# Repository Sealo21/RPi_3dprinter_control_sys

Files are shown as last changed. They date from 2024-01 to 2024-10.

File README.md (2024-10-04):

# RPi_3dprinter_control_sys
Environment controller for a 3D printing enclosure using a Raspberry Pi. \
Uses a temperature/VOC sensor and a custom PCB controller for the fans and strip LEDs controlled by a Raspberry Pi. \
This project is a work-in-progress. It is functional...but still a beta.

# Components
  - Raspberry Pi 4 Model B  
  - [Sensirion Particle, VOC, Humidity, and Temperature Sensor](https://www.sparkfun.com/products/23715)  
  - [waveshare 4 inch HDMI LCD 800x480](https://www.amazon.com/gp/product/B07P5H2315/)  
  - [Geekworm GPIO Extender](https://www.amazon.com/gp/product/B0BDF48FWM/)  
  - [SamIdea 2-Pack 40pin Male to Female IDC GPIO](https://www.amazon.com/gp/product/B07CGM83QL/)  
  - [Micro HDMI Cable](https://www.sparkfun.com/products/15796)  
  - Any 2 or 4 pin PC fan [I am using Noctua NF-A8 PWM](https://noctua.at/en/nf-a8-pwm)  
  - Any SMD5050 strip LED [LED Strip Lights](https://www.amazon.com/gp/product/B08JSQVBDQ/)

# Software Installation

[Install the latest version of Raspian OS](https://projects.raspberrypi.org/en/projects/raspberry-pi-setting-up) on your Raspberry Pi \
[Edit your configuration](https://www.raspberrypi.com/documentation/computers/configuration.html) to enable 'I2C' and 'Remote GPIO' under the interfaces tab \
Save and restart your RPi 

Update packages to the latest version:
```command line
sudo apt update
```

1. Download the files marked "RPi_3dprinter_control_sys_main" 
2. Locate the file 'main' in the folder 'dist' 
3. Edit the properties of 'main' to open with the program 'Terminal' 
4. Set the permission "Execute" to 'Anyone' 
5. If you run the program without modifying these settings a pop-up may occur asking to run the executable with an application 
6. Once these settings are confirmed the program should start with a terminal followed by a window

# Hardware Setup

A GPIO Extender will be needed to have the screen and GPIO be plugged in at the same time. 

There are a few options for the hardware of your controller \
A cheap option is to breadboard the design using the design schematics from the file 'LED_FAN_CONTROLLER.kicad_sch' \
You may need to download and install Kicad to view this schematic.

Here are the design requirements to breadboard this project:
- 4 [IRL520](https://www.digikey.com/en/products/detail/vishay-siliconix/IRL520PBF/811718) Mosfets as a substitute for the [IRLL014TRPBF](https://www.digikey.com/en/products/detail/vishay-siliconix/IRLL014TRPBF/811425)
- Wire for connections
- 6 10k Ohm resistors
- 5 1k Ohm resistors
- In testing phase for 3.3V power controller for breadboarding. I have been testing using an ADALM2000
- Using [TC74HC04APF](https://www.digikey.com/en/products/detail/toshiba-semiconductor-and-storage/TC74HC04APF/870457) for PWM operations in breadboard testing

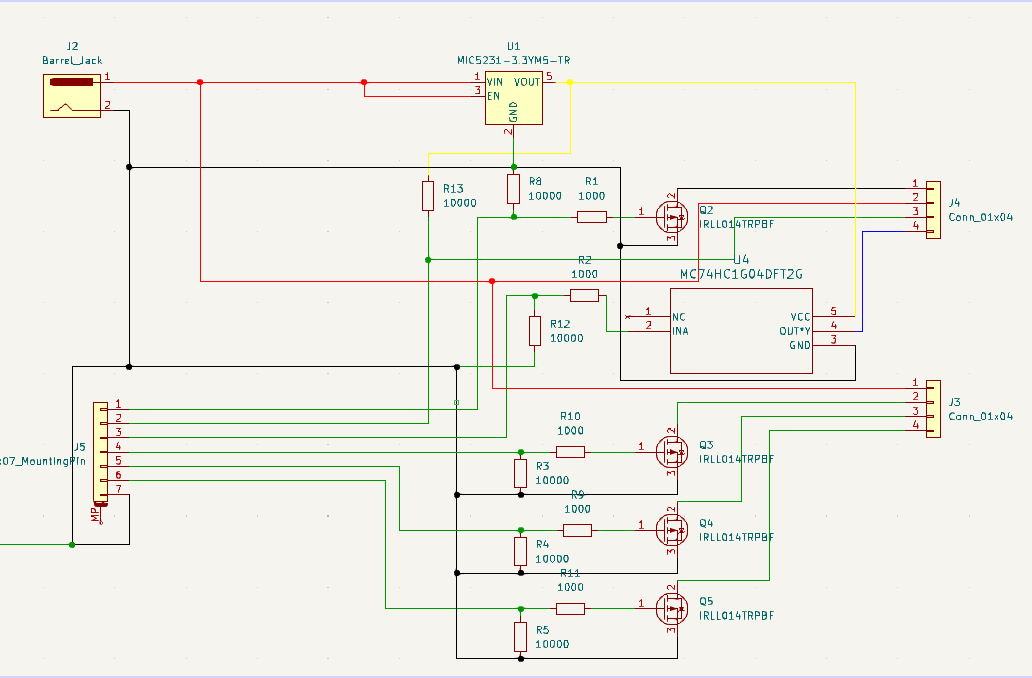
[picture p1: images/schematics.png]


The other option is to use the PCB schematics and manufacture the PCB. \
I have not done this yet as I am working on an upgrade to the current version.

# Touchscreen

Your experience may change based on which touchscreen is used. \
Use xinput-calibrator to calibrate the touch screen. 

```
sudo apt-get install xinput-calibrator
```
You will find this program under Menu -> Preferences -> Calibrate Touchscreen. \
Follow the instuctions given in the command line to save the calibration.

If the system does not recognize the touchscreen, check with the manufacturer for driver files. 

# Installing the Sen55 Sensor

The sensors I recieved do not have a standard coloring scheme. \
I have made a table below to list where the pins must go and their color.

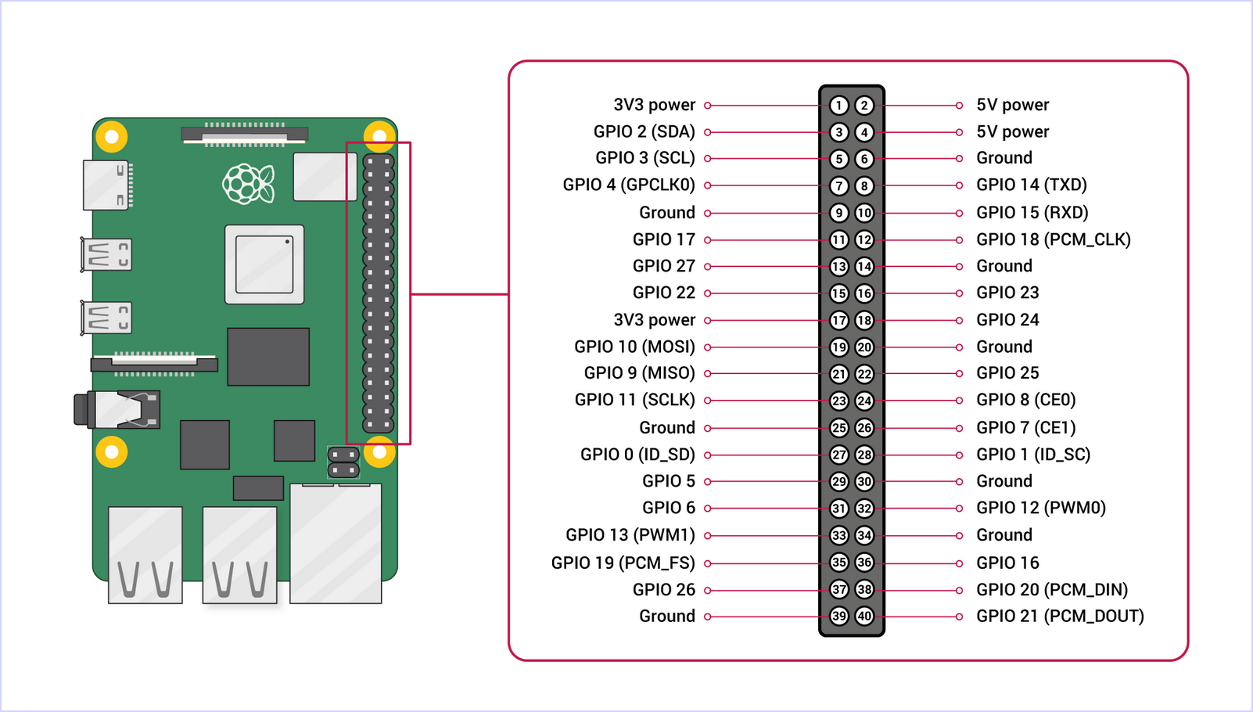
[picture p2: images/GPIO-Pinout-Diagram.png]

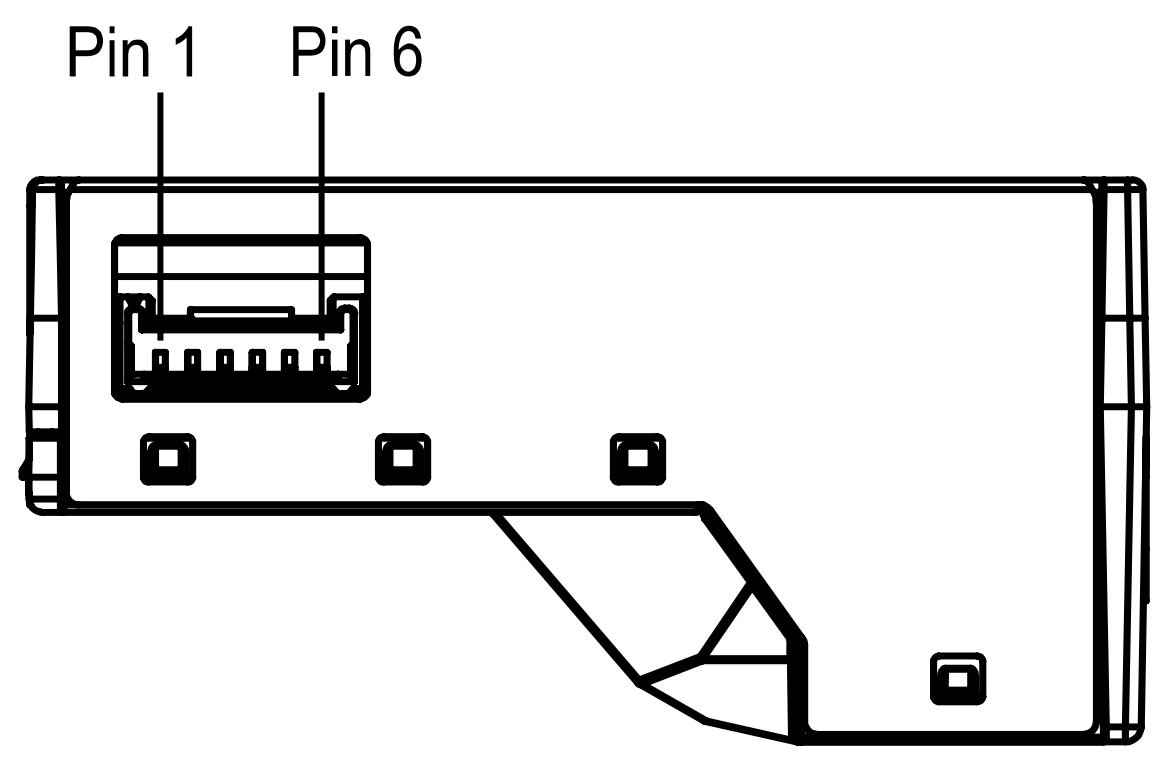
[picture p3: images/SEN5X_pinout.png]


|  Pin (On Sensor) |  Name |  Description |  Color  |  Pin Placement (On RPi)  |
| --- |:---:|:---:|:---:|:---:|
|  1 |  VCC | Supply Voltage  | Green |  Pin 2 (5V) |
|  2 |  GND | Ground | Blue |  Pin 6 (GND) |
|  3 |  SDA | I2C: Data | Yellow  |  Pin 3 (SDA) |
|  4 |  SCL | I2C: Clock | Black |  Pin 5 (SCL) |
|  5 |  SEL | Interface Select| Red |  Pin 9 (GND) |
|  6 |  NC | Do Not Connect  | Brown |  NC |

If the device is not recognized by the system, connect the VCC to 3.3V pin and then back to 5V. \
The device can function on both 3.3V and 5V but 5V is recommended by the manufacturer. \
Use the i2cdetect command to check connected I2C devices.

```command line
i2cdetect -y 1
```

You should see a device listed with a number value.

More information about this installation can be found [here](https://github.com/Sensirion/raspberry-pi-i2c-sen5x)

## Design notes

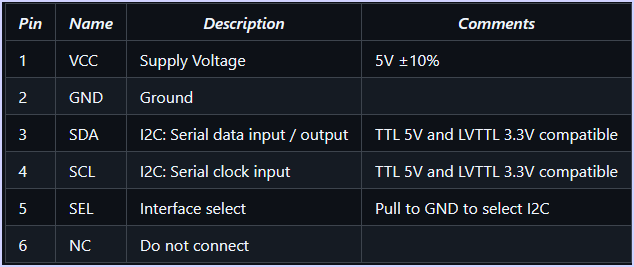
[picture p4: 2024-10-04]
images/Screenshot 2024-10-03 214042.png

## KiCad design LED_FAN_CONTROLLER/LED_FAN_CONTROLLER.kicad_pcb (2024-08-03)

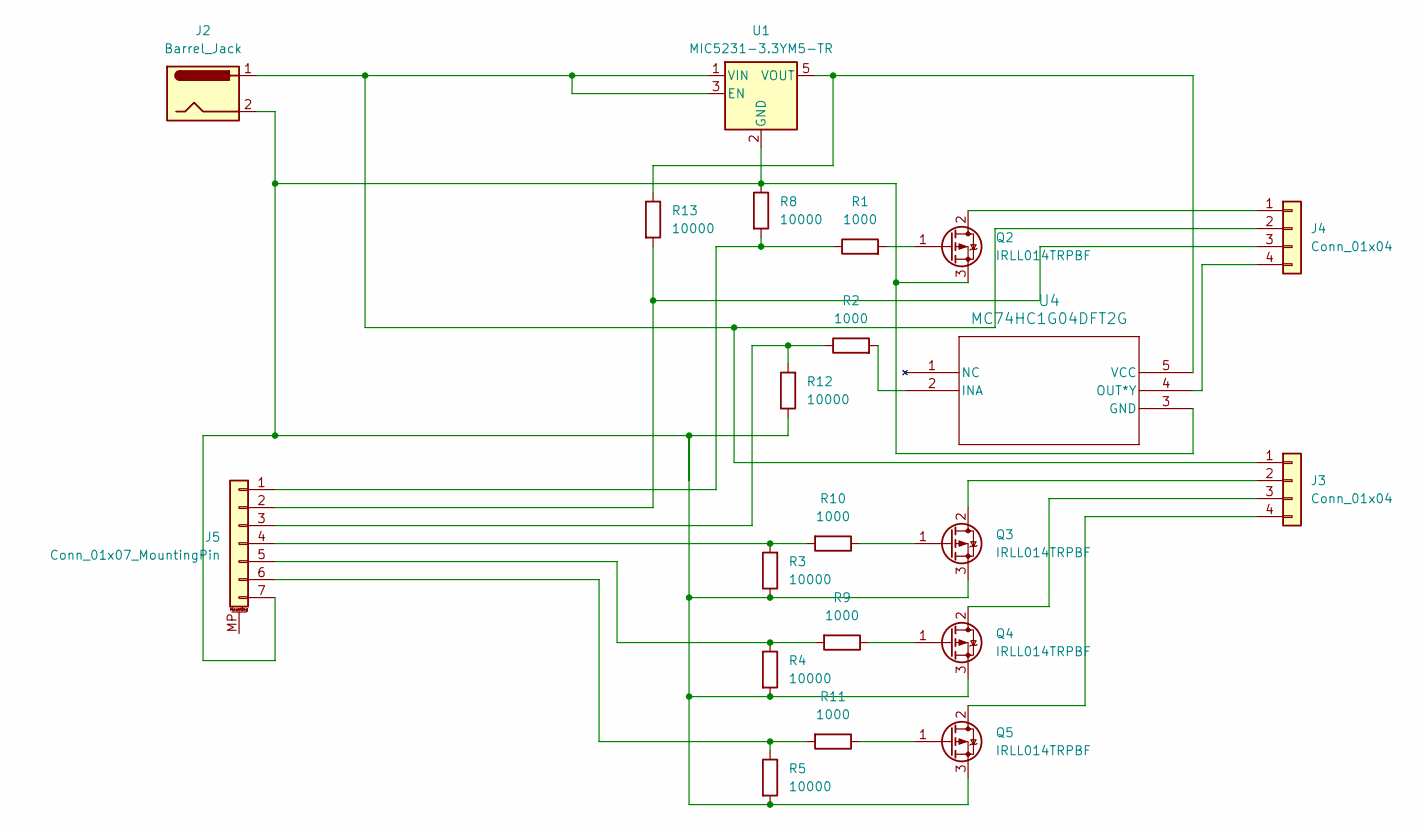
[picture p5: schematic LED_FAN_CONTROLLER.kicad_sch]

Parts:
J2: Barrel_Jack; BarrelJack_Horizontal
J3: Conn_01x04; PinHeader_1x04_P2.54mm_Horizontal
J4: Conn_01x04; FanPinHeader_1x04_P2.54mm_Vertical
J5: Conn_01x07_MountingPin; PinSocket_1x07_P2.54mm_Vertical
Q2, Q3, Q4, Q5: IRLL014TRPBF; SOT-223-3_TabPin2
R1, R2, R9, R10, R11: 1000; R_0603_1608Metric
R3, R4, R5, R8, R12, R13: 10000; R_0603_1608Metric
U1: MIC5231-3.3YM5-TR; SOT-23-5
U4: MC74HC1G04DFT2G; SC70-5_ONS

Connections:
unnamed: J2.1, J3.1, J4.2, U1.1 (VIN), U1.3 (EN)
unnamed: J3.2, Q3.2 (D)
unnamed: J3.3, Q4.2 (D)
unnamed: J3.4, Q5.2 (D)
unnamed: J4.1, Q2.2 (D)
unnamed 5: J4.3, J5.2, R13.2; also elsewhere on the board
unnamed 6: J4.4, U4.4 (OUT*Y); also elsewhere on the board
unnamed: J5.1, R1.1, R8.2
unnamed: J5.3, R2.1, R12.2
unnamed: J5.4, R3.2, R10.2
unnamed: J5.5, R4.1, R9.2
unnamed: J5.6, R5.1, R11.2
unnamed 12: J2.2, J5.7, Q2.3 (S), Q3.3 (S), Q4.3 (S), Q5.3 (S), R3.1, R4.2, R5.2, R8.1, R12.1, U1.2 (GND), U4.3 (GND); also elsewhere on the board
unnamed: Q2.1 (G), R1.2
unnamed: Q3.1 (G), R10.1
unnamed: Q4.1 (G), R9.1
unnamed: Q5.1 (G), R11.1
unnamed 17: R13.1, U1.5 (VOUT), U4.5 (VCC); also elsewhere on the board
unnamed: R2.2, U4.2 (INA)

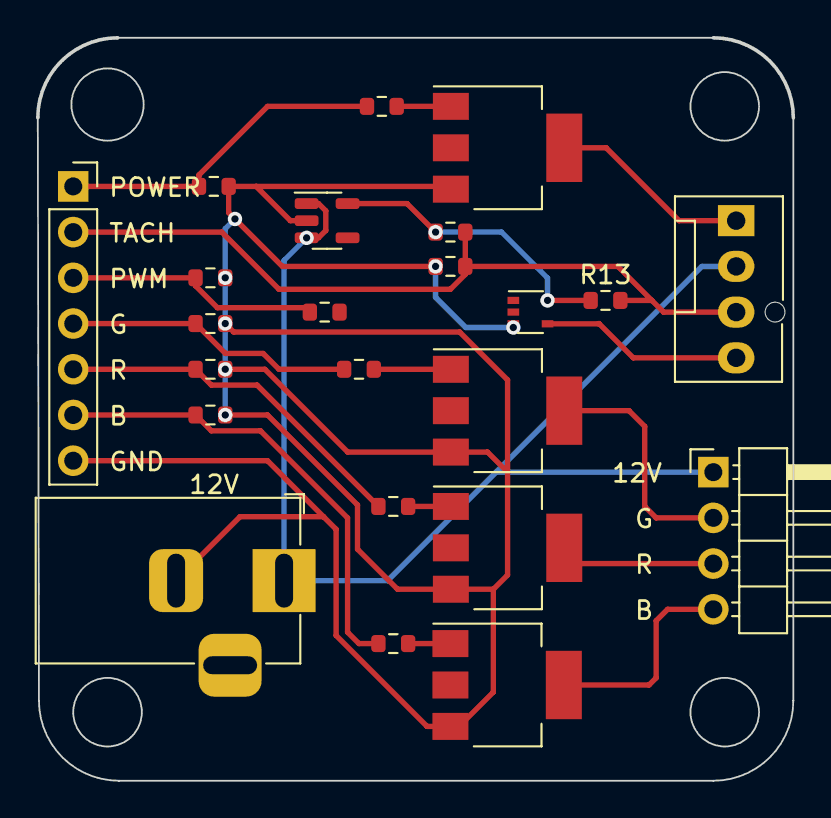
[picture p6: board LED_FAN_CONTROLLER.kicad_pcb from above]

Board: 2 copper layers, 42.0 x 41.3 mm, 23 parts (0 on the bottom side), 18 nets.

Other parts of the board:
R6: 1700; R_0603_1608Metric
R7: 3300; R_0603_1608Metric
U2: MC74HC1G04DFT2; SOT-353_SC-70-5

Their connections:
unnamed 5: R6.1, R7.1; also elsewhere on the board
unnamed 6: U2.4 (ON); also elsewhere on the board
unnamed 12: R7.2, U2.3 (FLAGB); also elsewhere on the board
unnamed 17: R6.2, U2.5 (VIN); also elsewhere on the board

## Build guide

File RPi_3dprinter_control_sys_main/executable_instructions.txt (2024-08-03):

source .venv/bin/activate # Need to add new Pip files for pyinstaller
pyinstaller --onefile <filename> # compile executable

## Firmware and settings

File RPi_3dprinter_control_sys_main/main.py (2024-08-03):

import PySimpleGUI as gui
import threading, time, subprocess, signal, sys, datetime, requests
from multiprocessing import Process, Pipe, Queue
from CollectData import collectData
import RPi.GPIO as GPIO
from configparser import ConfigParser
import os.path
import subprocess
import pigpio

# Global variables used in interrupts
lights_sig_on = False
light_timer = 0
lights_on = False
fans_on = False

def main():
	
	check_packages()
	config_setup()
	GPIO.setmode(GPIO.BOARD)
	
	# Declaration of variables used
	temperature_F = 0
	VOC = 0
	humidity = 0
	nox = 0
	
	# Interrupt global variables
	global lights_sig_on
	global light_timer
	
	# Config global variables
	global debug
	global fans_pwm
	global manual_timer_set_fans
	global manual_timer_set_lights
	global ntfy_channel
	global mobile_notifications
	global motion_detector
	global color
	
	# GPIO output
	global PI
	
	# Debugging variables
	global lights_on
	global fans_on
	global PWM
	global tach
	global light_color
	
	
	print_on = False
	notification_sent = False
	light_timer_active = False
	lights_manual_set = False
	fans_manual_set = False
	manual_light_timer = 0
	manual_fan_timer = 0
	ntfy_full_request = "https://ntfy.sh/"
	ntfy_on = False
	
	if mobile_notifications == True and ntfy_channel != "":
		ntfy_full_request = ntfy_full_request + ntfy_channel
		print("Notification channel" + ntfy_full_request)
		ntfy_on = True
		print("ntfy_on = " + str(ntfy_on))
	
	# Set keys for window layout
	VOC_safe = "SAFE"
	VOC_unsafe = "UNSAFE"

	key_lights_on = "Turn Lights On"
	key_lights_off = "Turn Lights Off"

	key_fans_on = "Turn Fans On"
	key_fans_off = "Turn Fans Off"
	
	key_print_start = "Start Print"
	key_print_end = "End Print"
	
	# Menu
	menu_def = [['File', ['Options', 'Exit']],
				['Help', 'About'], ]
	
	# Initial window layout
	layout = [
		#[gui.Menu(menu_def, )],
		[gui.Button(key_lights_on, size = (13, 3), button_color='red', font=("Arial", 20)),
		gui.Button(key_fans_on, size = (15, 3), button_color='red', font=("Arial", 20))],
		[gui.Text("Temperature (°F)", text_color="white", key = '-text-', background_color='black', font=("Roboto", 35))],
		[gui.Text(temperature_F, key = "tempF", text_color="blue", background_color='black', font=("Arial", 100)),
		gui.Text("°F", text_color="blue", key = '-text-', background_color='black', font=("Arial", 90))],
		[gui.Text("VOC", text_color="white", key = '-text-', background_color='black', font=("Arial", 45))],
		[gui.Text(VOC_safe,  key = "voc", text_color="green", background_color='black', font=("Arial", 90))],
		[gui.Text(VOC,  key = "voc_val", text_color="green", background_color='black', font=("Arial", 90))],
		[gui.Button(key_print_start, size = 8, button_color='green',  font=("Arial", 36)), gui.Button("Options", font=("Arial", 36))]
	]

	# Create the window
	gui.theme_background_color('black')
	window = gui.Window("Control Panel", layout, size=(480, 640),  element_justification='c').Finalize()
	window.Maximize()

	# Create an event loop
	while True:
		# Button event read
		event, value = window.read(timeout=0)
		backup_event = event
		backup_value = value
		
		# End program if user closes window
		if event == gui.WIN_CLOSED or event == 'Exit':
			if mobile_notifications == True and ntfy_on == True:
				#requests.post(ntfy_full_request, data="Program closing".encode(encoding='utf-8'))
				jim = 1
			break 
		
		if event == "Options":
			options_menu()
		
		# Collect data sent from sensor and parse
		if parent_conn.poll():
			data = parent_conn.recv()
		
			temperature_C = data[0] 
			temperature_F = round((temperature_C * 1.8) + 32) # Convert to Fahrenheit
			VOC = round(data[1])
			humidity = data[2]
			nox = data[3]
		
		# Get current minute of the hour
		current_time = datetime.datetime.now()
		now = current_time.minute
		
		# Send push notifications hourly of temperature/VOC levels
		if now == 0 and notification_sent == False and mobile_notifications == True and ntfy_on == True:
			status_notification(VOC, temperature_F, ntfy_full_request)
			notification_sent = True
		elif now == 1:
			notification_sent = False
		
		# Turn off manual settings when timer runs out
		if now == manual_light_timer:
			lights_manual_set = False
			
		if now == manual_fan_timer:
			fans_manual_set = False
		
			
		# Update data on window
		window["tempF"].update(temperature_F)
		window["voc_val"].update(VOC)
		
		
		# Change VOC display color on window to display safety
		if VOC > 150:
			window["voc"].update(VOC_unsafe, text_color="red")
			window["voc_val"].update(VOC, text_color="red")
		elif VOC < 150:
			window["voc"].update(VOC_safe, text_color="green")
			window["voc_val"].update(VOC, text_color="green")
		
		# Check if events were set manually
		if event == key_lights_on:
			lights_manual_set = True
			manual_light_timer = (now + 10)%60
		elif event == key_fans_on:
			fans_manual_set = True
			manual_fan_timer = (now + 10)%60
		
		# Turn lights off if timer is done
		if now >= light_timer and lights_on == True and lights_manual_set == False and light_timer_active == True:
			event = key_lights_on
			light_timer_active = False
		
		# Turn lights on if motion sensor detects movement
		if lights_sig_on == True and lights_on == False and lights_manual_set == False:
			event = key_lights_on
			lights_sig_on = False
			light_timer_active = True
		
		# Check if manual light button event took place
		if event == key_lights_on:
			if lights_on == True:
				lights_on = False
				change_light_color(light_color, False)
				window[key_lights_on].update(key_lights_on, button_color='red')
			else:
				lights_on = True
				change_light_color(light_color, True)
				window[key_lights_on].update(key_lights_off, button_color='green')
		
		# Restore event if changed earlier
		event = backup_event
		value = backup_value
		
		# Check temperature to change fan status
		if temperature_F < 80 and fans_on == True and fans_manual_set == False:
			event = key_fans_on
			setPWM(1000000) # fan off
		elif temperature_F >= 80 and fans_on == False and fans_manual_set == False:
			event = key_fans_on
			setPWM(750000) # set fan to 25% speed
		elif temperature_F >= 80 and temperature_F < 90 and fans_on == True and fans_pwm == True:
			setPWM(500000) # fans set 50% speed
		elif temperature_F >= 90 and temperature_F < 100 and fans_on == True and fans_pwm == True:
			setPWM(250000) # fans set 75% speed
		elif temperature_F >= 100 and fans_on == True and fans_pwm == True:
			setPWM(0) # fans set 100% speed
		
		# Check for status change from event
		if event == key_fans_on:
			if fans_on == True:
				fans_on = False
				GPIO.output(16, GPIO.LOW)
				window[key_fans_on].update(key_fans_on, button_color='red')
			else:
				fans_on = True
				GPIO.output(16, GPIO.HIGH)
				window[key_fans_on].update(key_fans_off, button_color='green')
			
		# Restore event if changed earlier
		event = backup_event
		value = backup_value	
			
		# Change button color and text when printing done
		if print_on == True and lights_on == False and light_timer_active == False and now >= light_timer + 5:
			event = key_print_start	
		
		# Check for a print event
		if event == key_print_start:
			if print_on == True:
				print_on = False
				if mobile_notifications == True and ntfy_on == True:
					notify()
				#GPIO.output(37, GPIO.LOW)
				window[key_print_start].update(key_print_start, button_color='green')
			else:
				print_on = True
				#GPIO.output(37, GPIO.HIGH)
				window[key_print_start].update(key_print_end, button_color='red')
		
	window.close()
	sys.exit(0)	

	
def notify(ntfy_full_request):
	
	# Function sends notification at the end of a printing cycle
	# Uses ntfy (ntfy.sh) to send push notifications to mobile app
	print("printing ended")
	#requests.post(ntfy_full_request, data="Printing Complete".encode(encoding='utf-8'))

def status_notification(VOC, temperature, ntfy_full_request):
	
	# Function called at beginning of every hour to show 
	# current temperature and VOC levels
	# Uses ntfy (ntfy.sh) to send push notifications to mobile app
	myObj = "VOC level = " + str(VOC) + ", Temperature = " + str(temperature) + "°F"
	requests.post(ntfy_full_request, data=myObj.encode(encoding='utf-8'))
	
def signal_handler(sig, frame):
	
	# Clean exit from program
	GPIO.cleanup()
	sys.exit()
	
def setPWM(dutyCycle):
	global PI
	global PWM
	if dutyCycle == 1000000:
		PI.hardware_PWM(12, 0, dutyCycle)
	else:
		PI.hardware_PWM(12, 25000, dutyCycle)
		
def change_light_color(color, on):
	# To add colors later just mix and match 
	# RGB values, only 8 total combinations
	# currently available
	if color == "white" and on == True:
		GPIO.output(11, GPIO.HIGH)
		GPIO.output(13, GPIO.HIGH)
		GPIO.output(15, GPIO.HIGH)
	elif color == "green" and on == True:
		GPIO.output(11, GPIO.HIGH)
		GPIO.output(13, GPIO.LOW)
		GPIO.output(15, GPIO.LOW)
	elif color == "red" and on == True:
		GPIO.output(11, GPIO.LOW)
		GPIO.output(13, GPIO.HIGH)
		GPIO.output(15, GPIO.LOW)
	elif color == "blue" and on == True:
		GPIO.output(11, GPIO.LOW)
		GPIO.output(13, GPIO.LOW)
		GPIO.output(15, GPIO.HIGH) 
	elif color == "lgreen" and on == True:
		GPIO.output(11, GPIO.HIGH)
		GPIO.output(13, GPIO.HIGH)
		GPIO.output(15, GPIO.LOW)
	elif color == "lblue" and on == True:
		GPIO.output(11, GPIO.HIGH)
		GPIO.output(13, GPIO.LOW)
		GPIO.output(15, GPIO.HIGH)
	elif color == "purple" and on == True:
		GPIO.output(11, GPIO.LOW)
		GPIO.output(13, GPIO.HIGH)
		GPIO.output(15, GPIO.HIGH)
	
	if on == False:
		GPIO.output(11, GPIO.LOW)
		GPIO.output(13, GPIO.LOW)
		GPIO.output(15, GPIO.LOW)         
	
def lights(callback):
	
	# Interrupt function when motion sensor detects motion
	# Sets global variable to True to notify main function that motion was detected
	# Only sets light_sig_on = True if the timer has already ran out
	# resets timer, takes into account hour reset
	global lights_sig_on
	global light_timer
	print("-------Motion Detected-------")
	time_set = datetime.datetime.now()
	if light_timer <= time_set.minute:
		lights_sig_on = True
	light_timer = (time_set.minute + 2)%60
	
def config_setup():
	# initializing global variables
	# if new config item is added, add a global variable
	# This variable will be the same as other later in section
	# global <new_item_name>
	global debug
	global fans_pwm
	global manual_timer_set_fans
	global manual_timer_set_lights
	global ntfy_channel
	global mobile_notifications
	global motion_detector
	global color
	global light_color
	
	dir_path = os.path.dirname(sys.executable)
	if getattr(sys, 'frozen', False):
		dir_path = os.path.dirname(sys.executable)
	elif __file__:
		dir_path = os.path.dirname(__file__)
	config_filepath = dir_path+"/config.ini"
	exists = os.path.exists(config_filepath)
	config = ConfigParser()
	
	if exists:
		print("-------Loading config-------")
		config.read(config_filepath)
	else:
		# When adding new items to config, may require generating new config
		# At the end of the list add items with syntax:
		# '<new_item_name>': "<default item value>",
		# <new_item_name> will be used in other sections
		print("-------Config file not found - generating default config-------")
		config['CONFIG'] = {
			'debug': False,
			'fans_pwm': False,
			'manual_timer_set_fans': 10,
			'manual_timer_set_lights': 10,
			'ntfy_channel': "",
			'mobile_notifications': False,
			'motion_detector': True,
			'color': "white",
		}
		with open("config.ini", "w") as output_file:
			config.write(output_file)
			
	# When adding new item to config, additional line at end required
	# syntax is just
	# <config_var_name> = config_data["<new_item_name>"]
	# <new_item_name> should be the same as the above section
	config_data = config["CONFIG"]
	debug = config_data["debug"]
	fans_pwm = config_data["fans_pwm"]
	manual_timer_set_fans = config_data["manual_timer_set_fans"]
	manual_timer_set_lights = config_data["manual_timer_set_lights"]
	ntfy_channel = config_data["ntfy_channel"]
	mobile_notifications = config_data["mobile_notifications"]
	motion_detector = config_data["motion_detector"]
	color = config_data["color"]
	light_color = config_data["color"]
	
	if debug == "True":
		debug = True
	else:
		debug = False
		
	if fans_pwm == "True":
		fans_pwm = True
	else:
		fans_pwm = False
		
	if mobile_notifications == "True":
		mobile_notifications = True
	else:
		mobile_notifications = False
		
	if motion_detector == "True":
		motion_detector = True
	else:
		motion_detector = False
		
	print("-------Loading Complete-------")
	
		
def options_menu():
	# initializing global variables in function
	# If new config item is added
	# add new global variable here too
	# global <new_item_name>
	global debug
	global fans_pwm
	global manual_timer_set_fans
	global manual_timer_set_lights
	global ntfy_channel
	global mobile_notifications
	global motion_detector
	global color
	global light_color
	
	
	# When adding item to options menu
	# create a key and name variable <new_item_name_layout>
	# fill in any other required info for layouts in pysimplegui
	# https://docs.pysimplegui.com/en/latest/documentation/module/layouts
	debug_layout = gui.Button("Off", key = "-DEBUG-", size = (10, 3),  button_color='red', font=("Arial", 13))
	if debug == True:
		debug_layout = gui.Button("On", key = "-DEBUG-", size = (10, 3),  button_color='green', font=("Arial", 13))
		
	fans_pwm_layout = gui.Button("Off", key = "-PWM-", size = (10, 3),  button_color='red', font=("Arial", 13))
	if fans_pwm == True:
		fans_pwm_layout = gui.Button("On", key = "-PWM-", size = (10, 3),  button_color='green', font=("Arial", 13))
		
	manual_timer_fans_layout = gui.Slider(range=(0, 30), key="-FTIMER-", enable_events=True, default_value = manual_timer_set_fans, orientation='h', s=(10, 15))
	manual_timer_lights_layout = gui.Slider(range=(0, 30), key="-LTIMER-", enable_events=True, default_value = manual_timer_set_lights, orientation='h', s=(10, 15))
	ntfy_channel_layout = gui.Input(ntfy_channel, key="-NTFY-", size = (10, 3))
	ntfy_confirm_layout = gui.Submit("Confirm", size = (10, 3))
	
	mobile_notifications_layout = gui.Button("Off", key = "-NOTIFICATIONS-", size = (10, 3),  button_color='red', font=("Arial", 13))
	if mobile_notifications == True:
		mobile_notifications_layout = gui.Button("On", key = "-NOTIFICATIONS-", size = (10, 3),  button_color='green', font=("Arial", 13))
		
	motion_detector_layout = gui.Button("Off", key = "-MOTION-", size = (10, 3),  button_color='red', font=("Arial", 13))
	if motion_detector== True:
		motion_detector_layout = gui.Button("On", key = "-MOTION-", size = (10, 3),  button_color='green', font=("Arial", 13))
	
	if color == "white":
		color_val = 0
	elif color == "green":
		color_val = 1
	elif color == "lgreen":
		color_val = 2
	elif color == "blue":
		color_val = 3
	elif color == "lblue":
		color_val = 4
	elif color == "purple":
		color_val = 5
	elif color == "red":
		color_val = 6
		
	color_layout = gui.Slider(range=(0, 6), key = "-COLOR-", disable_number_display = True, enable_events=True, default_value = color_val, orientation='h', size = (10, 15))
	
	# if new item added to config,
	# please add a <new_item_name_changed> to end of list
	# and increment range by 1
	changes_dict = {}
	debug_changed, fans_pwm_changed, manual_timer_set_fans_changed, manual_timer_set_lights_changed, ntfy_channel_changed, mobile_notifications_changed, motion_detector_changed, color_changed = (False for i in range(8))
	
	
	# Options layout
	# add new layouts created above here with any necessary text
	options_layout = [
					[gui.Text("Debug", text_color="white", font=("Arial", 15)), debug_layout, gui.Text("PWM", text_color="white", font=("Arial", 15)), fans_pwm_layout],
					#[],
					[gui.Text("Fan manual timer", text_color="white", font=("Arial", 15)), manual_timer_fans_layout],
					[gui.Text("Lights manual timer", text_color="white", font=("Arial", 15)), manual_timer_lights_layout],
					[gui.Text("Mobile Notifications", text_color="white", font=("Arial", 15)), mobile_notifications_layout],
					[gui.Text("ntfy_channel", text_color="white", font=("Arial", 15)), ntfy_channel_layout, ntfy_confirm_layout],
					[gui.Text("Motion detector", text_color="white", font=("Arial", 15)), motion_detector_layout],
					[gui.Text("LED color", text_color = "white", font=("Arial", 15)), color_layout],
					[gui.Button("Close", key = "-sac-", button_color='gray', font=("Arial", 20))]]
	
	option_window = gui.Window("Options", options_layout, size=(480, 750), resizable = True).Finalize()
	#option_window.Maximize()
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

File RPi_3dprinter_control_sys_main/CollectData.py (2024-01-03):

import time
from smbus2 import SMBus, i2c_msg
from struct import unpack
from multiprocessing import Process, Pipe

def CrcCalculator(data):
    """
        Constructs a calculator object with the given CRC parameters.
        :param int width:
            Number of bits of the CRC (e.g. 8 for CRC-8).
        :param int polynomial:
            The polynomial of the CRC, without leading '1' (e.g. 0x31 for the
            polynomial x^8 + x^5 + x^4 + 1).
        :param int init_value:
            Initialization value of the CRC. Defaults to 0.
        :param int final_xor:
            Final XOR value of the CRC. Defaults to 0.
    """
    width = 8
    polynomial = 0x31
    final_xor = 0x00
    crc = 0xFF
    for value in data:
        crc ^= value
        for i in range(width):
            if crc & (1 << (width - 1)):
                crc = (crc << 1) ^ polynomial
            else:
                crc = crc << 1
            crc &= (1 << width) - 1
    return crc ^ final_xor


def sendData(child_conn, temp, VOC, humidity, nox):
    child_conn.send([temp, VOC, humidity, nox])

def collectData(child_conn):
    # I2C bus 1 on a Raspberry Pi 3B+
    # SDA on GPIO2=Pin3 and SCL on GPIO3=Pin5
    #   sensor +3.3V at Pin1 and GND at Pin6
    DEVICE_BUS = 1

    # device address SEN55
    DEVICE_ADDR = 0x69
    # init I2C
    bus = SMBus(DEVICE_BUS)

    # wait 1 s for sensor start up (> 1000 ms according to datasheet)
    time.sleep(1)

    #Read status of the STAR engine
    msg = i2c_msg.write(DEVICE_ADDR, [0x60, 0xB2])
    bus.i2c_rdwr(msg)

    # wait 10 ms for data ready
    time.sleep(0.01)

    # read 9 bytes in as a sequence of MSB, LSB, CRC
    # offset, slope. time constant
    msg = i2c_msg.read(DEVICE_ADDR, 9)
    bus.i2c_rdwr(msg)

    # merge byte 0 and byte 1 to integer
    t_offset  = int(unpack(">h", msg.buf[0:2])[0]) #different method choosen here due to the possible negative sign in parameter
    t_slope  = (msg.buf[3][0] << 8 | msg.buf[4][0])
    t_time  = (msg.buf[6][0] << 8 | msg.buf[7][0])

    # wait 10 ms for data ready
    time.sleep(0.01)

    #Set new values:
    t_offset = int(-5 * 200)
    t_slope = int(0.01 * 10000)
    t_time = int(10 * 60)

    data = []
    data.append((t_offset & 0xff00) >> 8)
    data.append(t_offset & 0x00ff)

    data.append((t_slope & 0xff00) >> 8)
    data.append(t_slope & 0x00ff)

    data.append((t_time & 0xff00) >> 8)
    data.append(t_time & 0x00ff)

    msg = i2c_msg.write(
        DEVICE_ADDR,
        [0x60, 0xB2,
        data[0], data[1], CrcCalculator(data[0:2]),
        data[2], data[3], CrcCalculator(data[2:4]),
        data[4], data[5], CrcCalculator(data[4:6])]
    )
    bus.i2c_rdwr(msg)

    # wait 10 ms for data ready
    time.sleep(0.01)

    #Read status of the STAR engine
    msg = i2c_msg.write(DEVICE_ADDR, [0x60, 0xB2])
    bus.i2c_rdwr(msg)

    # wait 10 ms for data ready
    time.sleep(0.01)

    # read 3 bytes in as a sequence of MSB, LSB, CRC
    # status
    msg = i2c_msg.read(DEVICE_ADDR, 9)
    bus.i2c_rdwr(msg)

    # merge byte 0 and byte 1 to integer
    t_offset = int(unpack(">h", msg.buf[0:2])[0]) #different method choosen here due to the possible negative sign in parameter
    t_slope = (msg.buf[3][0] << 8 | msg.buf[4][0])
    t_time = (msg.buf[6][0] << 8 | msg.buf[7][0])

    # wait 10 ms for data ready
    time.sleep(0.01)

    # start scd measurement in periodic mode, will update every 2 s
    msg = i2c_msg.write(DEVICE_ADDR, [0x00, 0x21])
    bus.i2c_rdwr(msg)

    # wait for first measurement to be finished
    time.sleep(2)

    # repeat read out of sensor data
    while True:
        msg = i2c_msg.write(DEVICE_ADDR, [0x03, 0xC4])
        bus.i2c_rdwr(msg)

        # wait 1 ms for data ready
        time.sleep(0.01)

        # read 12 bytes; each three bytes in as a sequence of MSB, LSB, CRC
        # co2, temperature, rel. humidity, status
        msg = i2c_msg.read(DEVICE_ADDR, 24)
        bus.i2c_rdwr(msg)

        # merge byte 0 and byte 1 to integer
        # co2 is in ppm
        pm1p0 = (msg.buf[0][0] << 8 | msg.buf[1][0])/10
        pm2p5 = (msg.buf[3][0] << 8 | msg.buf[4][0])/10
        pm4p0 = (msg.buf[6][0] << 8 | msg.buf[7][0])/10
        pm10p0 = (msg.buf[9][0] << 8 | msg.buf[10][0])/10

        # merge byte 3 and byte 4 to integer
        temp = msg.buf[15][0] << 8 | msg.buf[16][0]
        # calculate temperature  according to datasheet
        temp /= 200

        # merge byte 6 and byte 7 to integer
        humidity = msg.buf[12][0] << 8 | msg.buf[13][0]
        # calculate relative humidity according to datasheet
        humidity /= 100

        VOC = (msg.buf[18][0] << 8 | msg.buf[19][0]) / 10
        nox = (msg.buf[21][0] << 8 | msg.buf[22][0]) / 10
        
        sendData(child_conn, temp, VOC, humidity, nox)
        
        # print(VOC)
        # print(temp)
        # wait 2 s for next measurement
        time.sleep(2)
    
    child_conn.close()
    bus.close()
